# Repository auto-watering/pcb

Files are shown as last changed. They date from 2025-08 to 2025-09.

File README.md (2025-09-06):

# Auto Watering PCB

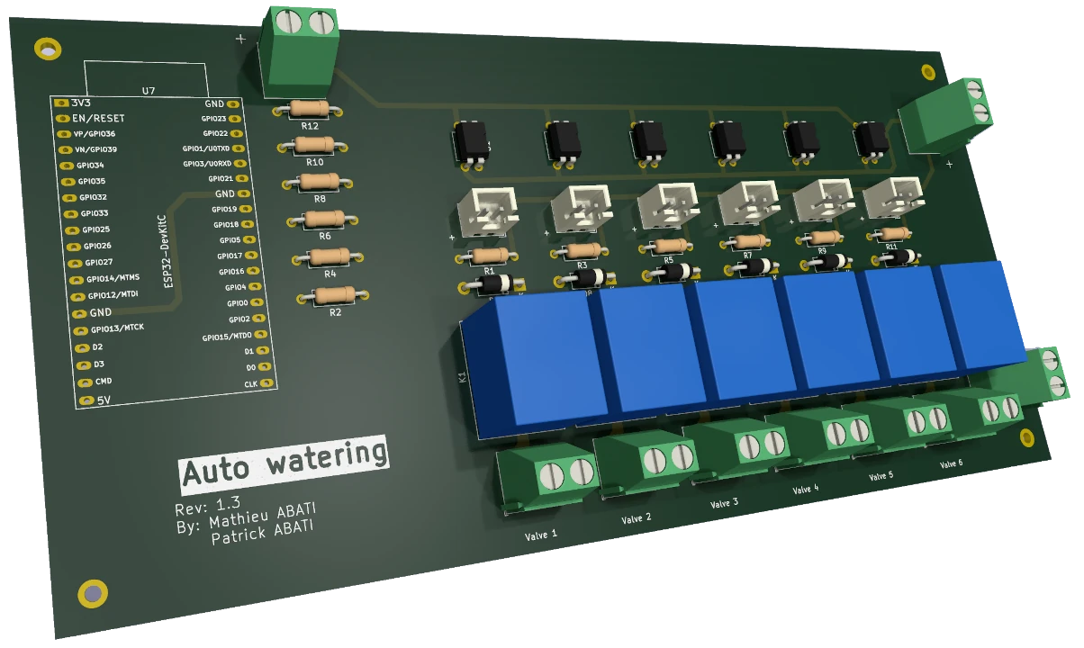
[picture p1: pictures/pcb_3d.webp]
PCB 3D view


KiCad project for auto watering PCB.
This PCB is designed for up to 6 valves.

This KiCad project requires Espressif KiCad Library.

You can find a firmware designed to run on this board [on the dedicated repository](https://github.com/auto-watering/firmware).

## Required parts

- ESP32 DevKit C
- Support for ESP32 board
- For each valve:
  - SRD12VDC relay
  - EL817(D)-G or PC817 C photocoupler
  - LED
  - JST connector 1x02 2.50mm pitch (for case mounted LED)
  - 1 kOhm resistor
  - 56 Ohm resistor
  - flyback diode
  - TerminalBlock Phoenix MKDS-1,5/2 1x02 5mm pitch (for valve)
  - Valves themselves (for example RainBird HV series, 24VAC)
- 5V DC power supply for ESP32
- 12V DC power supply for relays command
- Power supply for valves (24VAC for RainBird HV series)
- 3x TerminalBlock Phoenix MKDS-1,5/2 1x02 5mm pitch (for power supplies)

## Prototyping

Thanks to [PCBWay](https://www.pcbway.com) for helping prototyping this project
by sending me assembled boards !
The build quality is great, and their manufacturing service was very available
and professional to help me to prepare everything and create the bill of
material (BOM).

Below are some pictures of these prototypes boards.

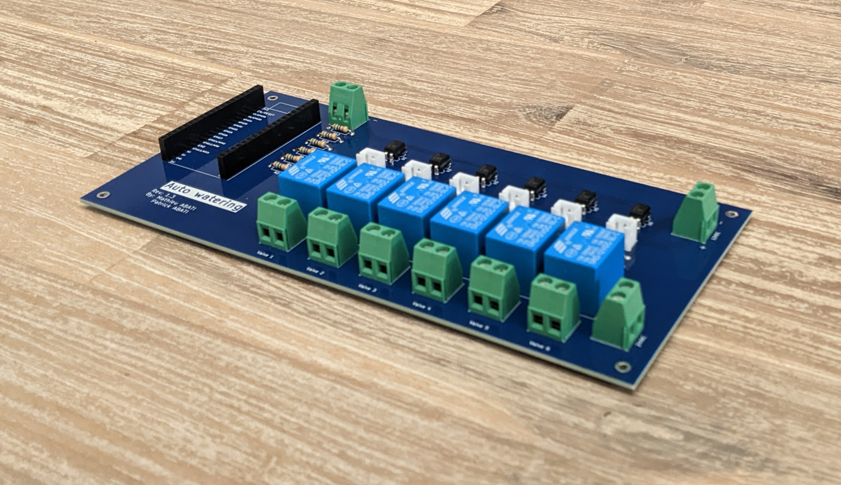
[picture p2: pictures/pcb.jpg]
PCB view


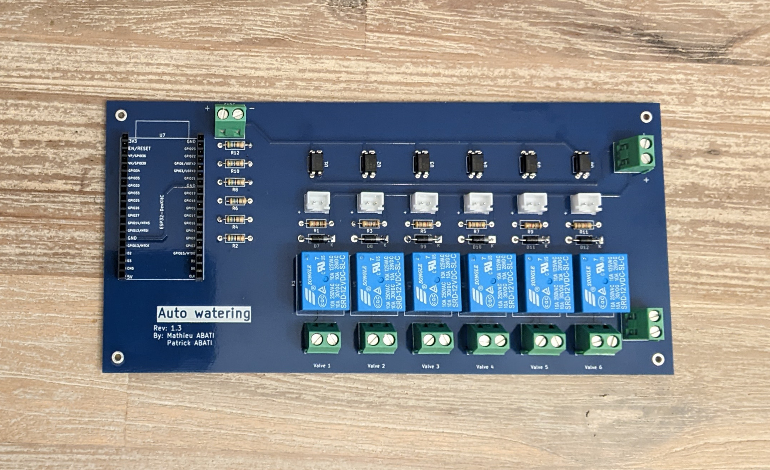
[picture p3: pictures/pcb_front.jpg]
PCB front view


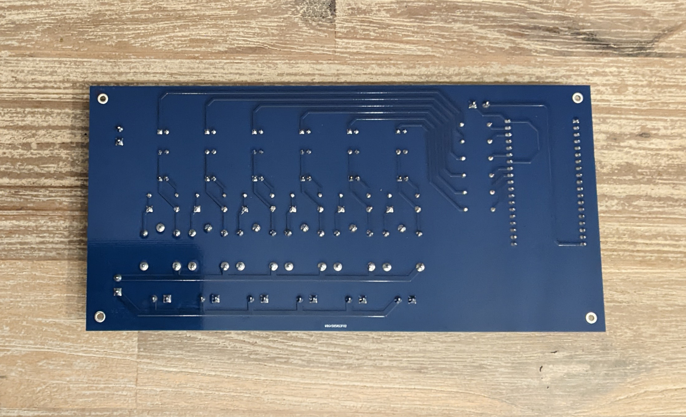
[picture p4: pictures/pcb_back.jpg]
PCB back view


You can find in the project releases all [PCBWay](https://www.pcbway.com)
related resources to make it (gerbers, positions, BOM).

It is perfectly working, installed in a waterproof case, with power supplies
for 5VDC, 12VDC, 24VAC, and the ESP32 with the
[firmware](https://github.com/auto-watering/firmware).

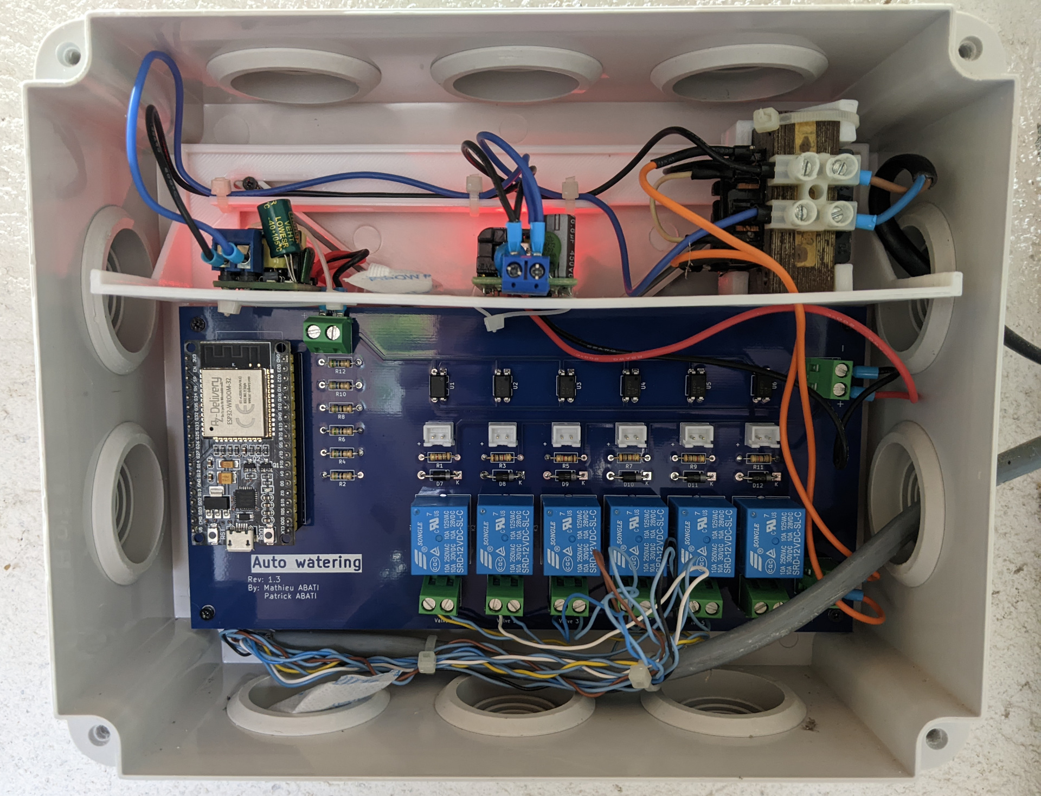
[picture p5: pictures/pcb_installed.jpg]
PCB installed view


## Improvements

As EL817(D)-G optocoupler should be OK to control the relay coil, it may be
appropriate to use a MOFSET between them.

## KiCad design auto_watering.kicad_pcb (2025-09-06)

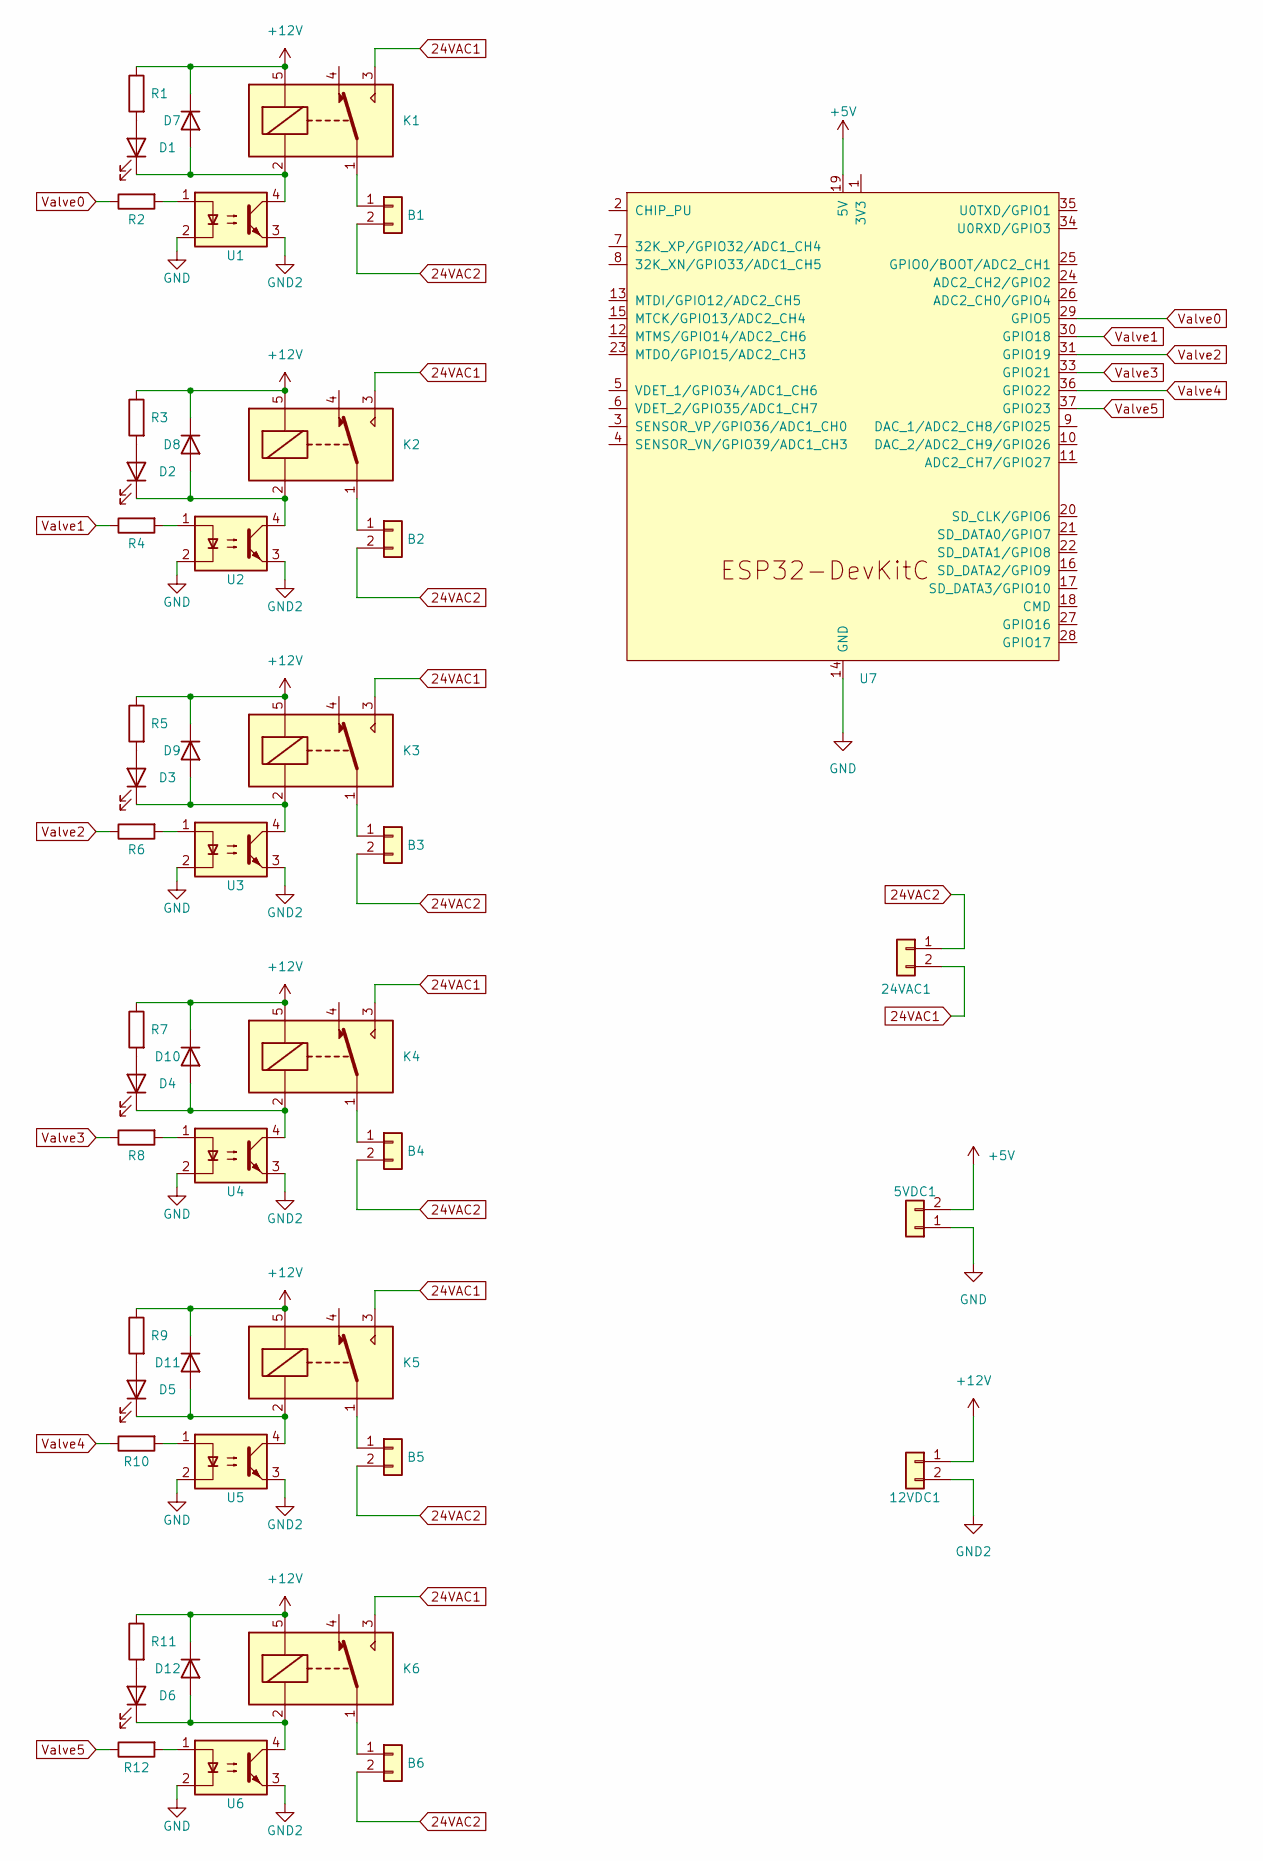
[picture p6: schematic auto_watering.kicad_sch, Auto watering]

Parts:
5VDC1, 12VDC1, 24VAC1: Conn_01x02; TerminalBlock_Phoenix_MKDS-1,5-2_1x02_P5.00mm_Horizontal
B1, B2, B3, B4, B5, B6: Conn_01x02; TerminalBlock_Phoenix_MKDS-1,5-2_1x02_P5.00mm_Horizontal
D1, D2, D3, D4, D5, D6: LED; JST_XH_B2B-XH-A_1x02_P2.50mm_Vertical
D7, D8, D9, D10, D11, D12: 1N4004; D_DO-41_SOD81_P10.16mm_Horizontal
K1, K2, K3, K4, K5, K6: SRD12VDC; Relay_SPDT_SANYOU_SRD_Series_Form_C
R1, R3, R5, R7, R9, R11: 1K; R_Axial_DIN0207_L6.3mm_D2.5mm_P10.16mm_Horizontal
R2, R4, R6, R8, R10, R12: 56; R_Axial_DIN0207_L6.3mm_D2.5mm_P10.16mm_Horizontal
U1, U2, U3, U4, U5, U6: PC817; DIP-4_W7.62mm
U7: ESP32-DevKitC

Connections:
24VAC1: 24VAC1.2, K1.3, K2.3, K3.3, K4.3, K5.3, K6.3
24VAC2: 24VAC1.1, B1.2, B2.2, B3.2, B4.2, B5.2, B6.2
+5V: 5VDC1.2, U7.19 (5V)
+12V: 12VDC1.1, D7.1 (K), D8.1 (K), D9.1 (K), D10.1 (K), D11.1 (K), D12.1 (K), K1.5, K2.5, K3.5, K4.5, K5.5, K6.5, R1.1, R3.1, R5.1, R7.1, R9.1, R11.1
GND: 5VDC1.1, U1.2, U2.2, U3.2, U4.2, U5.2, U6.2, U7.14 (GND), U7.32 (GND), U7.38 (GND)
GND2: 12VDC1.2, U1.3, U2.3, U3.3, U4.3, U5.3, U6.3
unnamed: B1.1, K1.1
unnamed: B2.1, K2.1
unnamed: B3.1, K3.1
unnamed: B4.1, K4.1
unnamed: B5.1, K5.1
unnamed: B6.1, K6.1
unnamed: D1.2 (A), R1.2
unnamed: D1.1 (K), D7.2 (A), K1.2, U1.4
unnamed: D2.2 (A), R3.2
unnamed: D2.1 (K), D8.2 (A), K2.2, U2.4
unnamed: D3.2 (A), R5.2
unnamed: D3.1 (K), D9.2 (A), K3.2, U3.4
unnamed: D4.2 (A), R7.2
unnamed: D5.2 (A), R9.2
unnamed: D6.2 (A), R11.2
unnamed: D4.1 (K), D10.2 (A), K4.2, U4.4
unnamed: D5.1 (K), D11.2 (A), K5.2, U5.4
unnamed: D6.1 (K), D12.2 (A), K6.2, U6.4
unnamed: R2.2, U1.1
unnamed: R4.2, U2.1
unnamed: R6.2, U3.1
unnamed: R8.2, U4.1
unnamed: R10.2, U5.1
unnamed: R12.2, U6.1
Valve0: R2.1, U7.29 (GPIO5)
Valve1: R4.1, U7.30 (GPIO18)
Valve2: R6.1, U7.31 (GPIO19)
Valve3: R8.1, U7.33 (GPIO21)
Valve4: R10.1, U7.36 (GPIO22)
Valve5: R12.1, U7.37 (GPIO23)

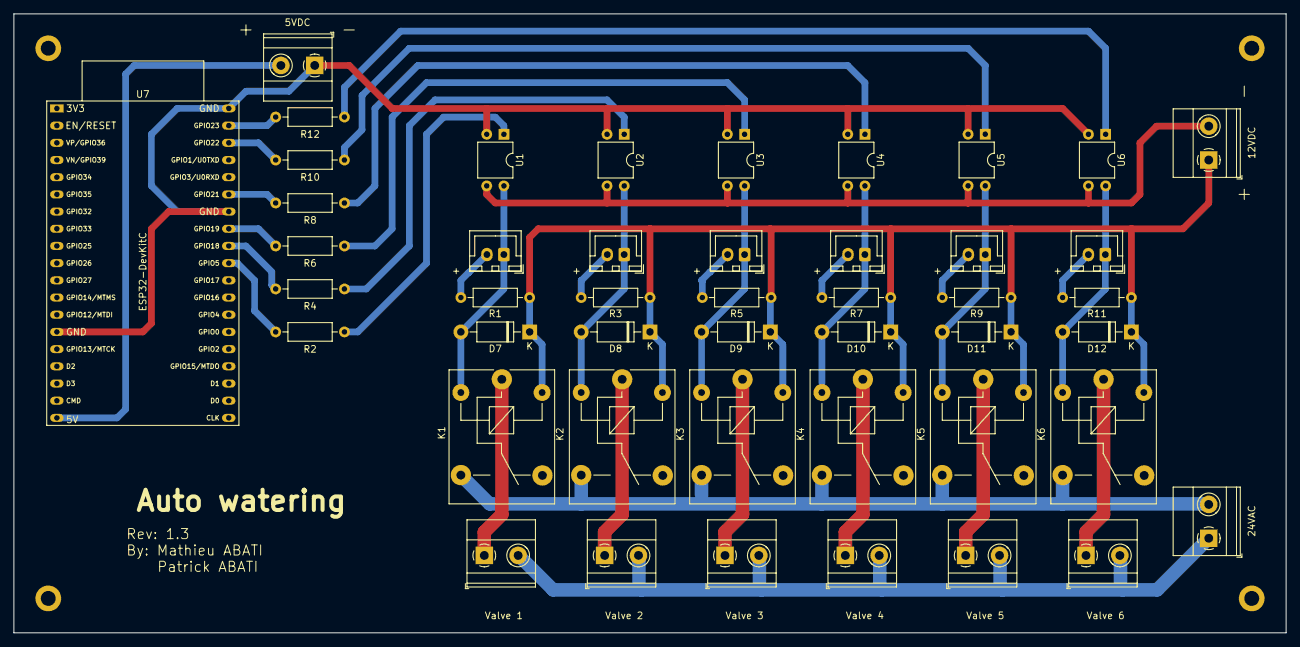
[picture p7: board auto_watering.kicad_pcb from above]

Board: 2 copper layers, 188.0 x 91.4 mm, 46 parts (0 on the bottom side), 36 nets.

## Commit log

2025-08-09 Release KiCad files
    [auto_watering.csv, auto_watering.kicad_pcb, auto_watering.kicad_sch]
2025-08-09 Add PCB 3D view picture
2025-09-04 Update README and add pictures
    [auto_watering.csv]
2025-09-05 Add remark about optocoupler and relay coil control
2025-09-06 Add photocoupler reference used in PCBWay BOM
2025-09-06 Remove JLC marking on PCB
    [auto_watering.kicad_pcb]
